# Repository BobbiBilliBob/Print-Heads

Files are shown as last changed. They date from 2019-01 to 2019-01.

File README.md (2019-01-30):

# Print-Heads

## PH_4010
It's a print head for 4010 fans. 

## PH_4010_BLTouch
It's a print head for 4010 fans. This version provides possibility to install BLTouch.
We install this version on printers that we produce by default.

## PH_Sunon35x5_original
It's a print head for Sunon35x5 mm fans. 

## PH_Sunon35x7
It's a print head for Sunon35x5 mm fans. 

# License
Z Bolt printer is released under the [GNU General Public License v3.0.](https://opensource.org/licenses/GPL-3.0)

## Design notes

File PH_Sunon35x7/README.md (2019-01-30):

# Print-Head

Version of print head for the Sunon 35x7mm fans.
This folder contains only those parts that differ from the version for the fans Sunon 35x5mm.
So please find other parts in folder PH_Sunon35x5_Original.

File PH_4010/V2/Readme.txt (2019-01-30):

-Подкорректированы некоторые размеры
-Добавлена полка для вентилятора радиатора
-Добавлена верхняя заглушка вентилятора радиатора
-Крепление E3dv6 оптимизировано под вентилятор 4010 (спасибо @AleksRei)

Винты крепления вентилятора радиатора - М3х16 потай.

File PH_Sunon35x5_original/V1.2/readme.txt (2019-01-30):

разнес пошире "дюзы" обдува детали, чтобы не плавились нагревательным "кубиком". Остальные детали не изменились.

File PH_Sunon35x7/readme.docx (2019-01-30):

Остальные печатные детали такие же, как в версии PH_Sunon35x5_ORIGINAL

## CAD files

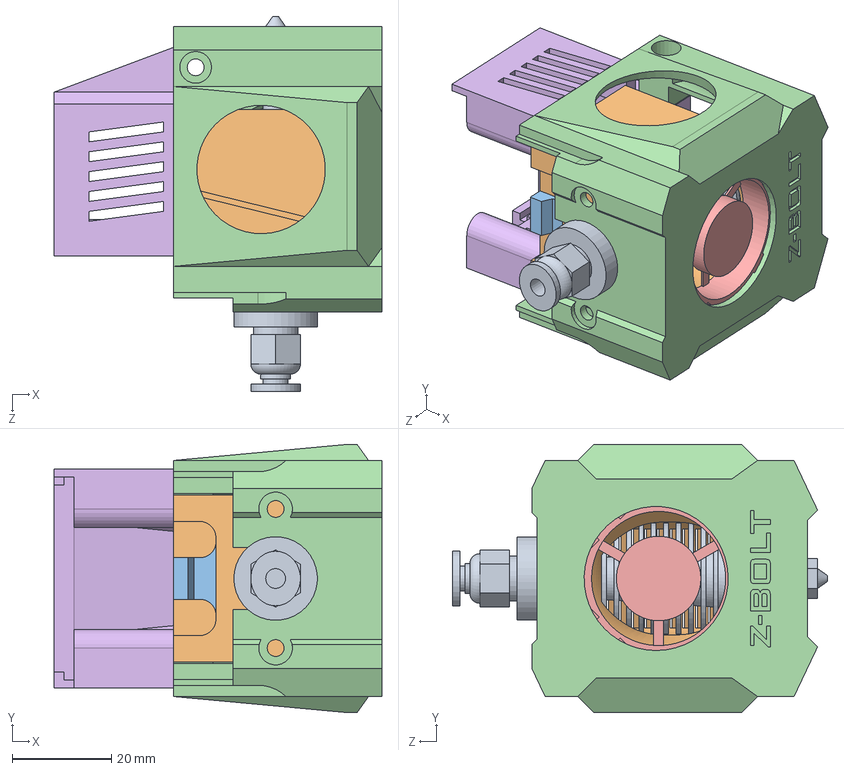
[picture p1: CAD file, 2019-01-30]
PH_Sunon35x5_original/AS_PH_35x5.SLDASM
66.0 x 54.0 x 75.5 mm
e3dv6
e3dv6Mount
fix
PHFront
cooler30-7
PHback

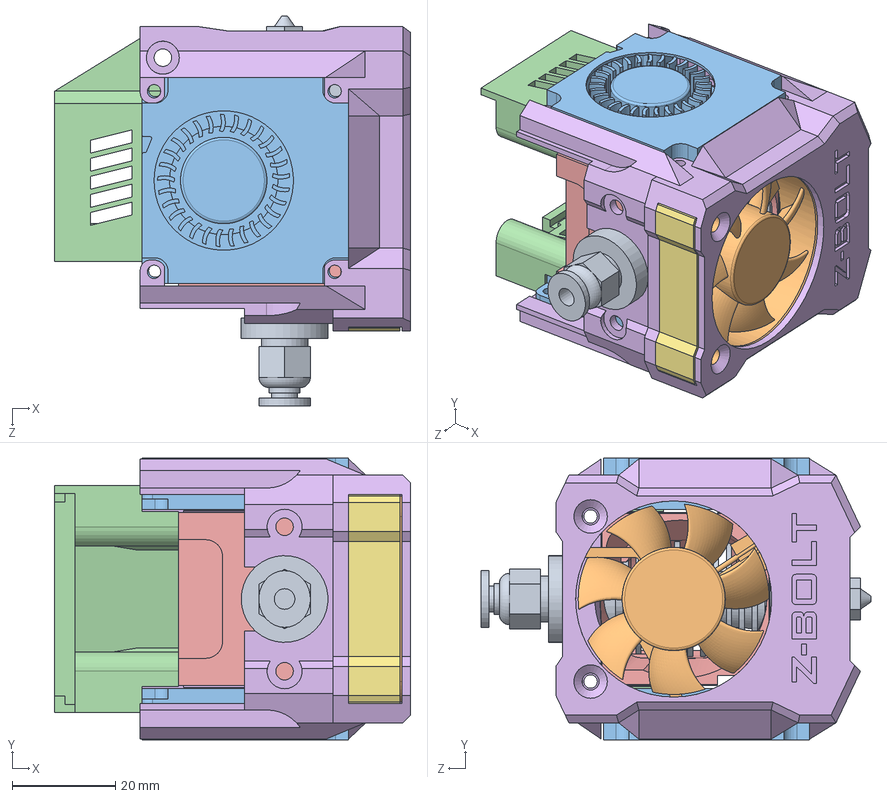
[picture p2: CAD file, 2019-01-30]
PH_4010/V2/src/AS_PH4010_V2.SLDASM
69.0 x 54.6 x 75.5 mm
e3dv6
40x40x10 DC Fan
4010turbo x 2
PHback4010
e3dv6Mount4010
PHFront_4010_V2
VentCover

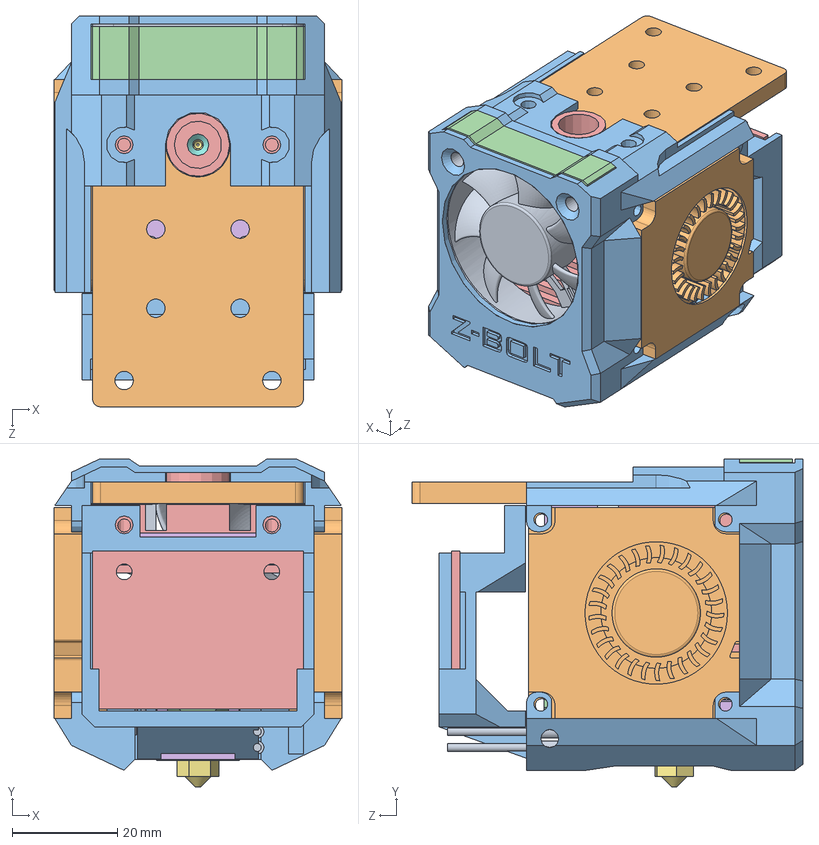
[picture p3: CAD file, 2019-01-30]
PH_4010_custom_radiator/AS_PH4010_V4.SLDASM
54.6 x 62.2 x 74.1 mm
40x40x10 DC Fan
4010turbo x 2
PHFront_4010_V4
VentCover
CustomRadiatorV4
Heatblock
nuzzle
Heatbr
heater
HotEndPlate
PHback4010V4_2
Деталь2
pcb
Костыль А

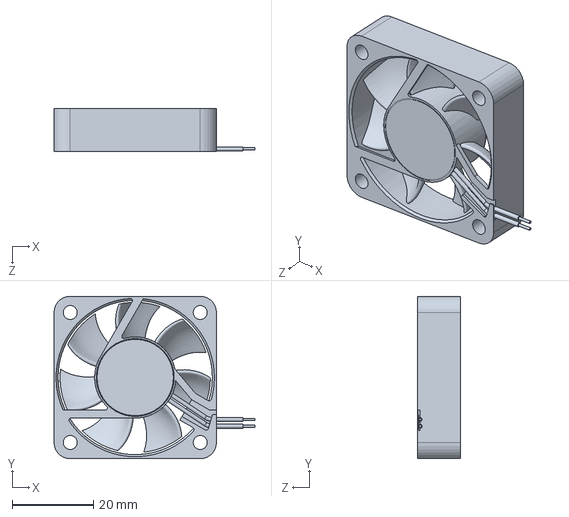
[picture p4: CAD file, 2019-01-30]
PH_4010/V2/src/40x40x10 DC Fan.SLDPRT
49.5 x 40.0 x 10.5 mm

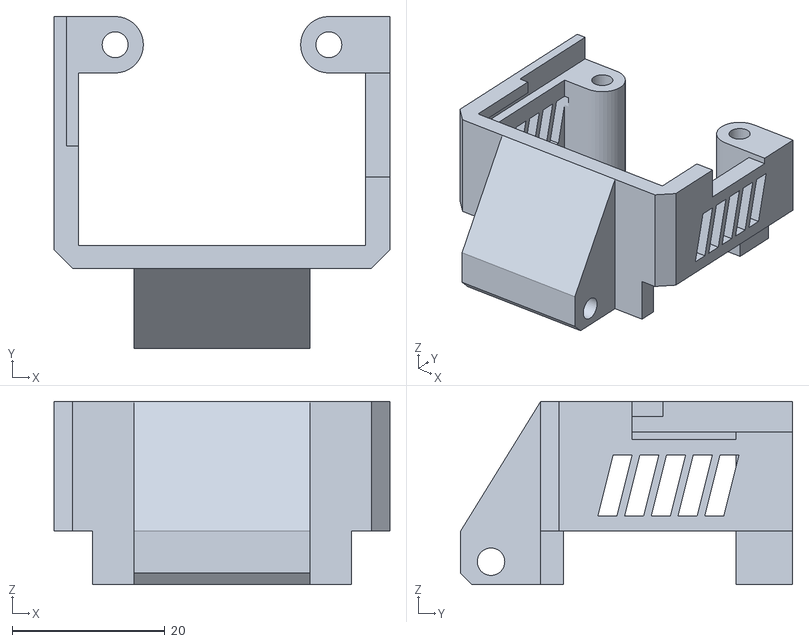
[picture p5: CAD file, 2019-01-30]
PH_4010/V2/STL/PHback4010.STL
44.0 x 43.5 x 24.0

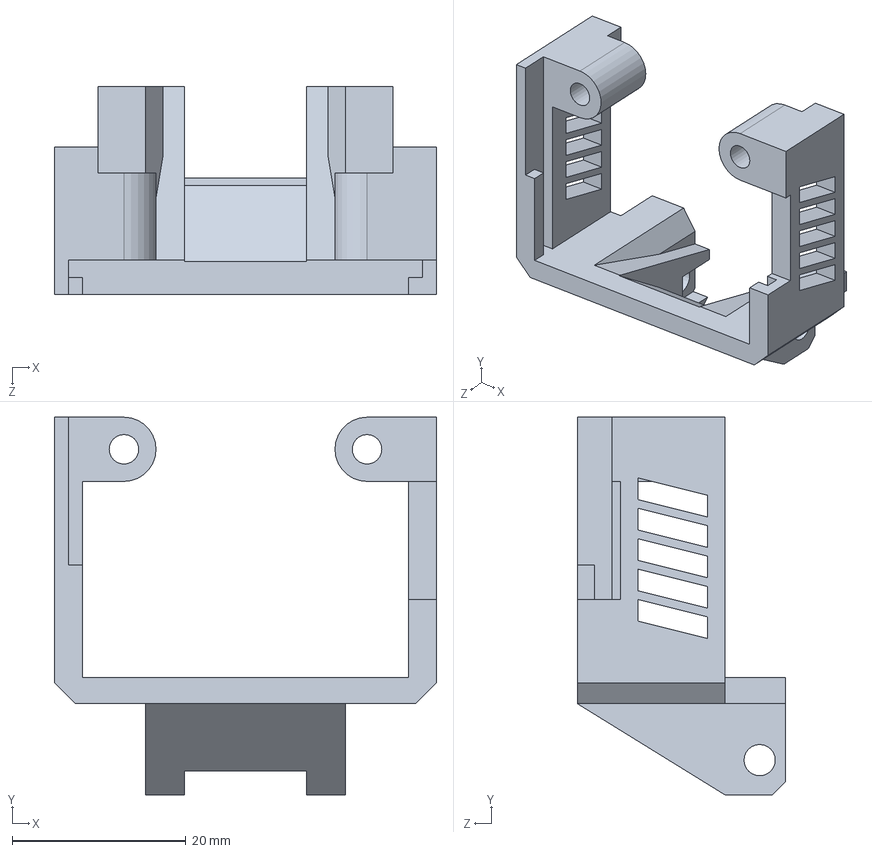
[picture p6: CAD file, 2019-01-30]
PH_4010_BLTouch (from @mivtahim )/src/PHback4010.SLDPRT
44.0 x 43.5 x 24.0 mm

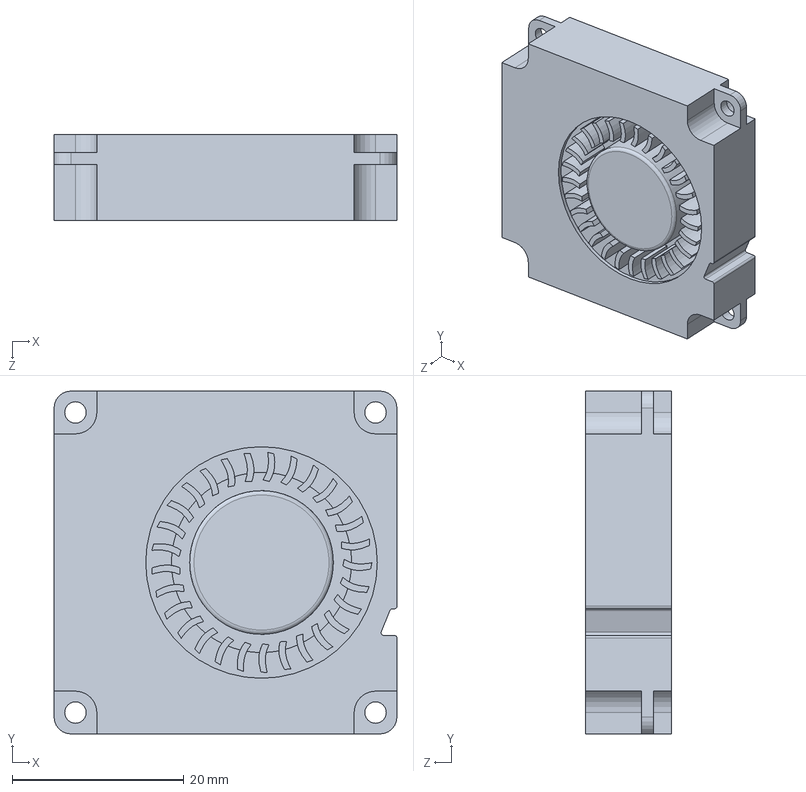
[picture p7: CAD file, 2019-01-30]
PH_4010_custom_radiator/4010turbo.SLDPRT
40.0 x 40.0 x 10.0 mm

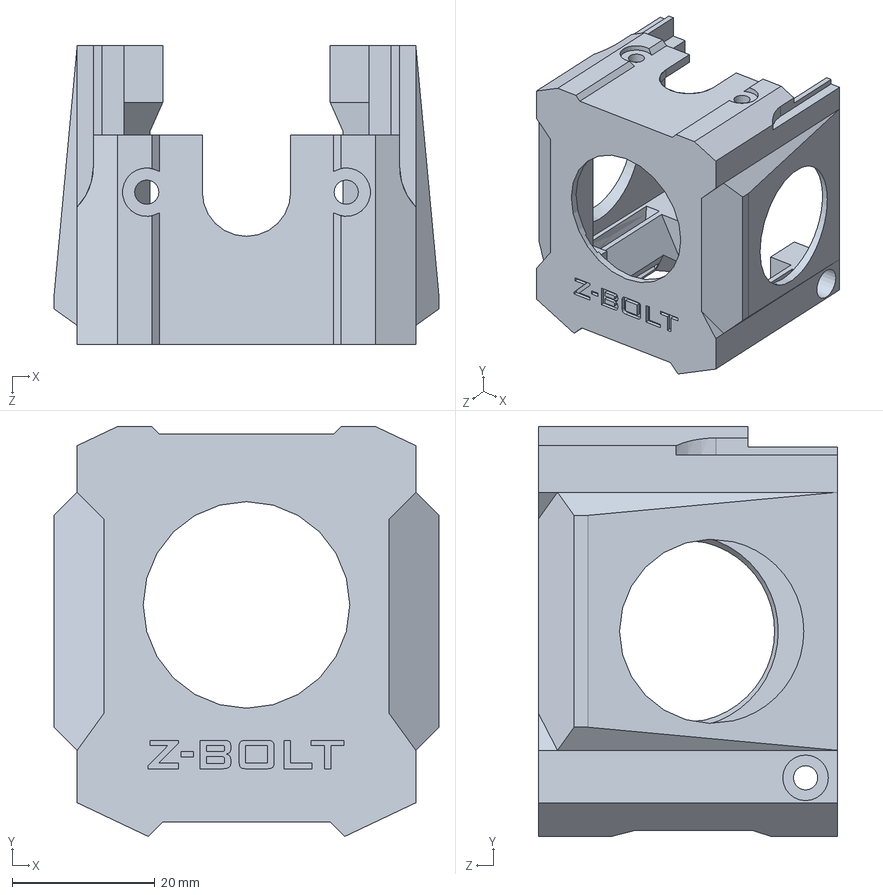
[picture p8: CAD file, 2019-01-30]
PH_Sunon35x5_original/V1.2/PHFront_V1.2.SLDPRT
54.0 x 57.5 x 42.0 mm

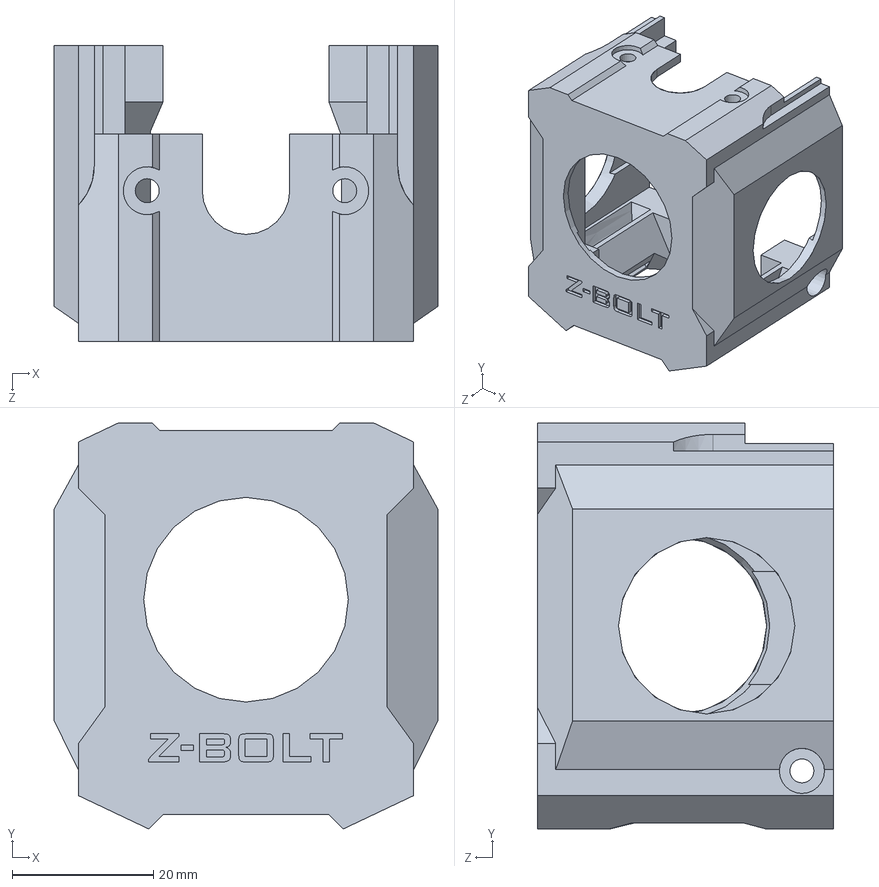
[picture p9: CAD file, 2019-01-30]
PH_Sunon35x7/PHFront_Sunon7mm.SLDPRT
54.4 x 57.5 x 42.0 mm

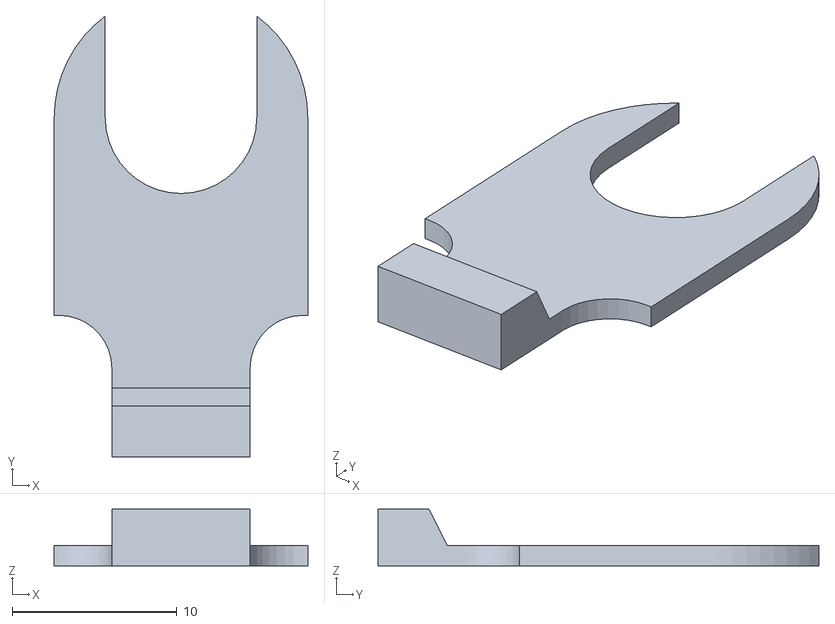
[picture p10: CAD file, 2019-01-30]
PH_4010/V2/STL/fix.STL
15.4 x 26.8 x 3.44

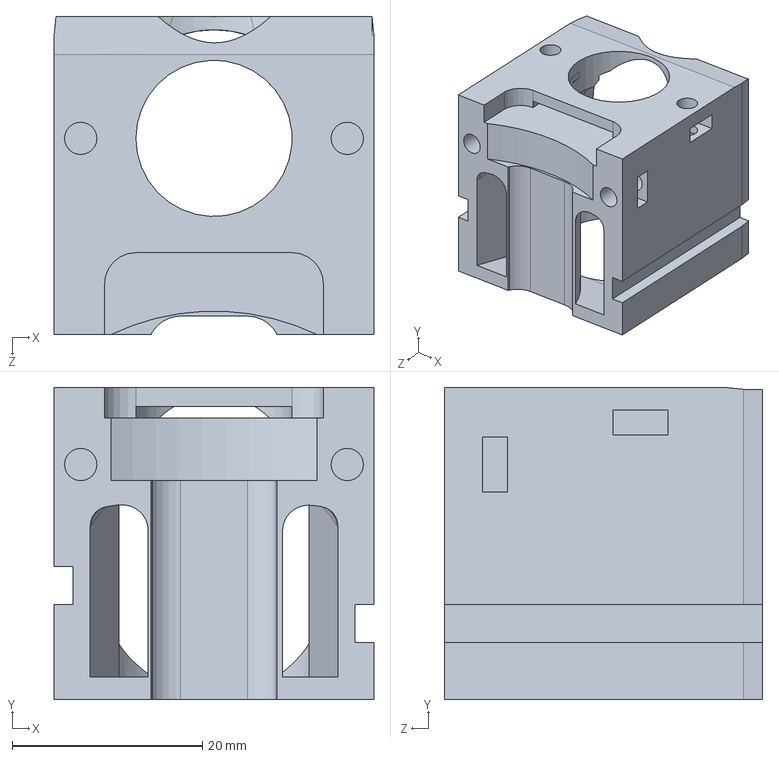
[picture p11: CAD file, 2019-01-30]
PH_4010_BLTouch (from @mivtahim )/src/e3dv6Mount4010.SLDPRT
33.6 x 32.8 x 33.4 mm

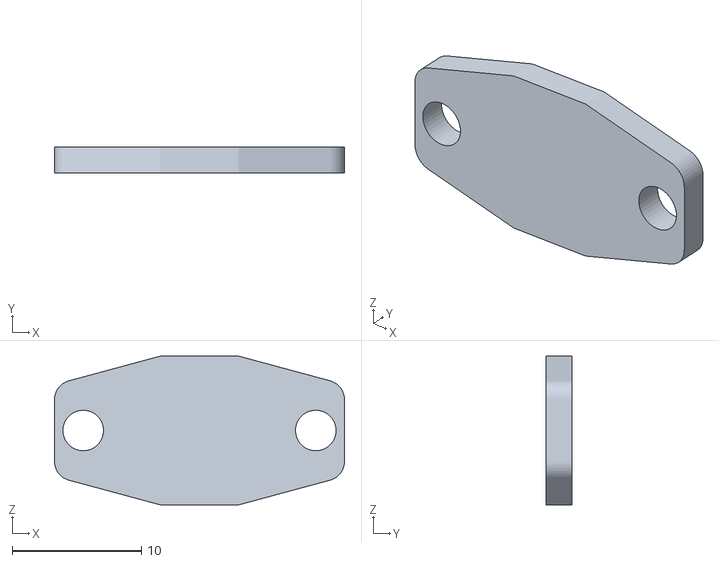
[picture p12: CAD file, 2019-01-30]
PH_4010_BLTouch (from @mivtahim )/STL/opravka_A_v2.STL
22.4 x 2.00 x 11.5

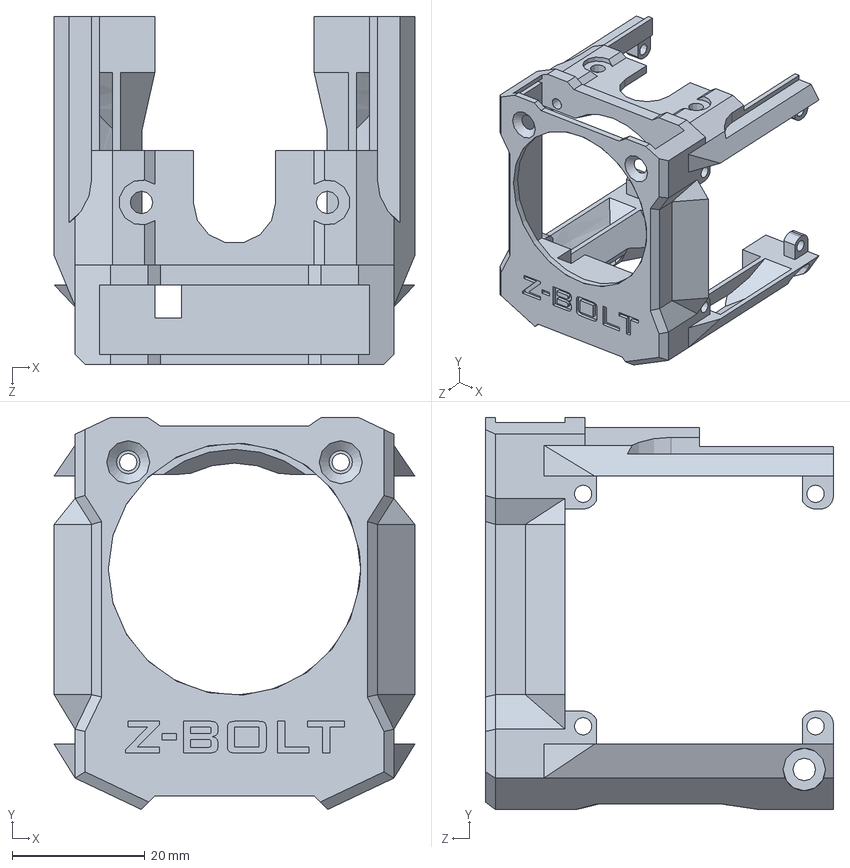
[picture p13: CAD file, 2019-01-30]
PH_4010_custom_radiator/PHFront_4010_V4.SLDPRT
54.3 x 59.0 x 52.4 mm

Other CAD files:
PH_4010_BLTouch (from @mivtahim )/STL/BLTPH_PHback4010.STL
PH_4010/V2/src/PHback4010.SLDPRT
PH_Sunon35x5_original/PHFront.SLDPRT
PH_4010/V2/STL/PHFront_4010_V2.STL
Old Versions/PH_Sunon35x7 v0.1/PHback.STL
Old Versions/PH_Sunon35x7 v0.1/fix.STL
PH_4010/V1/STL/PHFront_4010.STL
PH_4010/V1/STL/e3dv6Mount4010.STL
PH_4010/V1/src/AS_PH4010.SLDASM
PH_4010/V1/src/PHFront_4010.SLDPRT
PH_4010/V1/src/PHback4010.SLDPRT
PH_4010/V1/src/e3dv6.SLDPRT
PH_4010/V1/src/e3dv6Mount4010.SLDPRT
PH_4010/V1/src/fix.SLDPRT
PH_4010/V2/STL/VentCover.STL
PH_4010/V2/STL/e3dv6Mount4010.STL
PH_4010/V2/src/PHFront_4010_V2.SLDPRT
PH_4010/V2/src/VentCover.SLDPRT
PH_4010/V2/src/e3dv6.SLDPRT
PH_4010/V2/src/e3dv6Mount4010.SLDPRT
PH_4010/V2/src/fix.SLDPRT
PH_4010_BLTouch (from @mivtahim )/STL/BLTPH_Holder.STL
PH_4010_BLTouch (from @mivtahim )/STL/BLTPH_PHFront_4010_V2.STL
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

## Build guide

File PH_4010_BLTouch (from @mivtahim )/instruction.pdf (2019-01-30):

1. СБОРКА

Модель "opravka_A_v2" (на скрине не конкретно она, но принцип сохраняется) необходима для срезания ушей с корпуса сенсора:

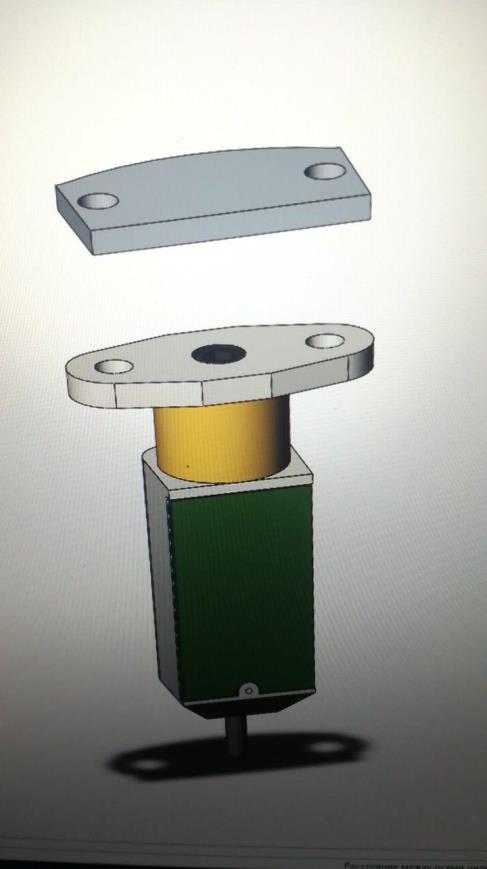
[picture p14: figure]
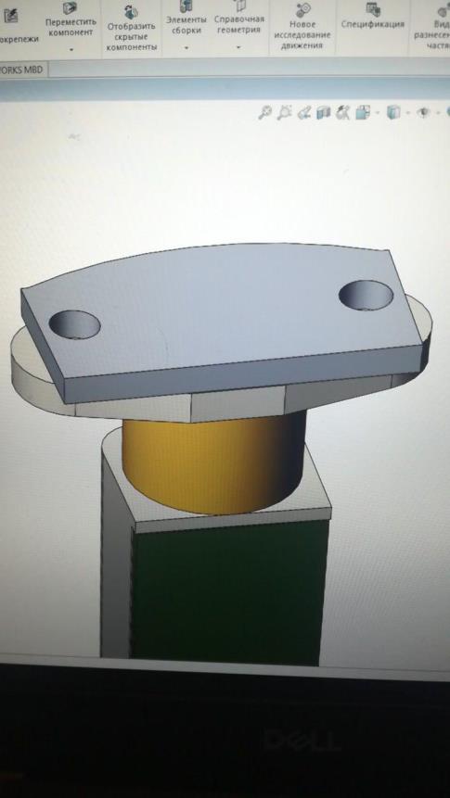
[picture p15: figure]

Центруем и как следует затягиваем, не до скрипа, конечно. Но чтоб не сместилась:

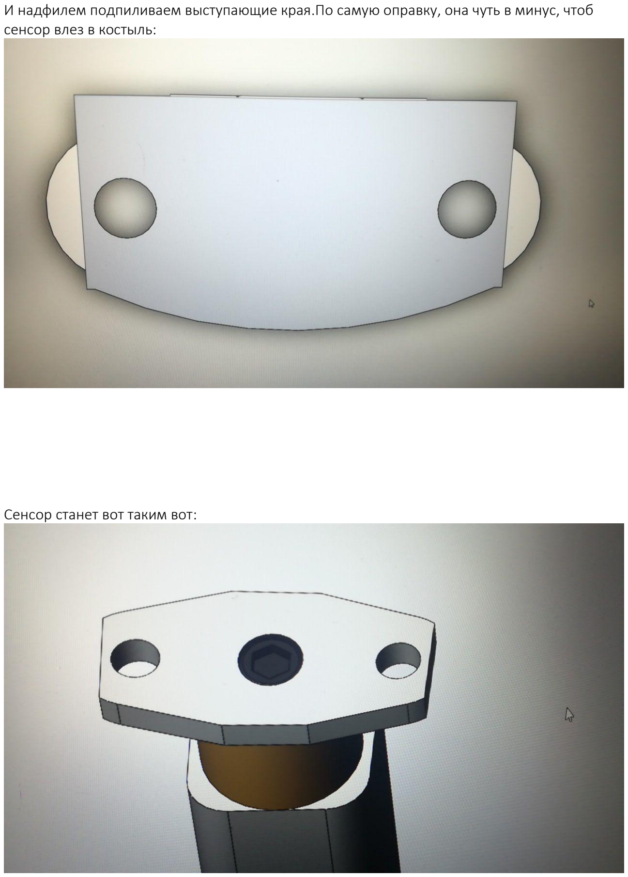
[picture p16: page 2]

И надфилем подпиливаем выступающие края.По самую оправку, она чуть в минус, чтоб сенсор влез в костыль:

Сенсор станет вот таким вот:

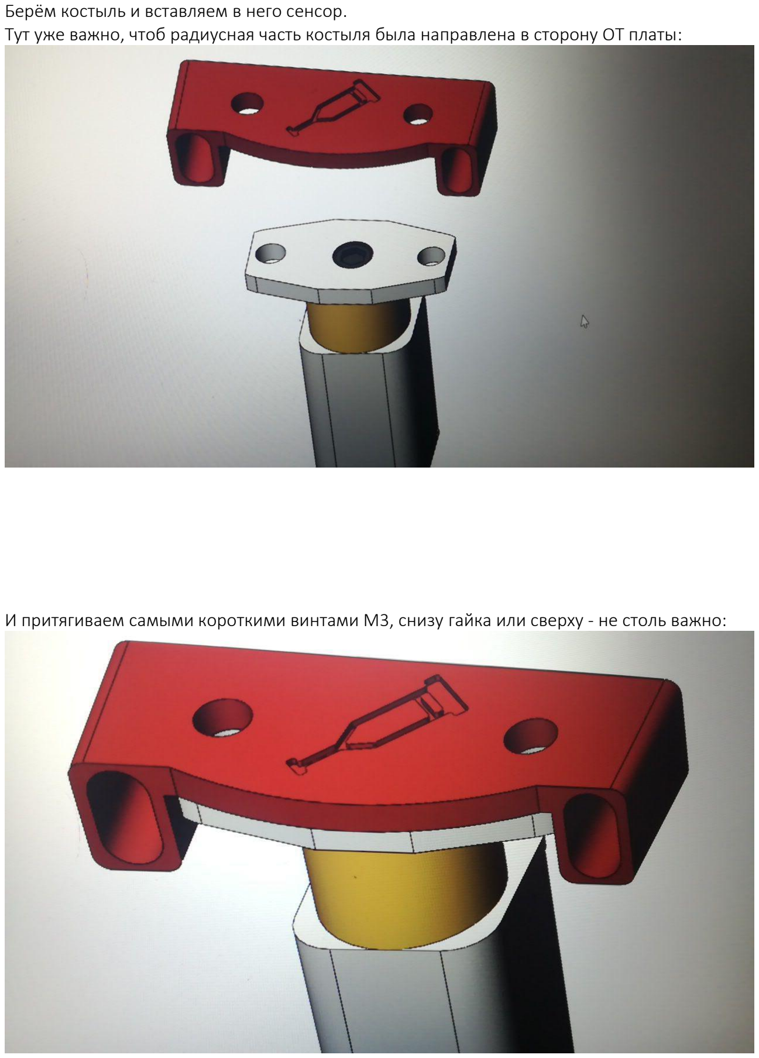
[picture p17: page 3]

Берём костыль и вставляем в него сенсор.
Тут уже важно, чтоб радиусная часть костыля была направлена в сторону ОТ платы:

И притягиваем самыми короткими винтами М3, снизу гайка или сверху - не столь важно:

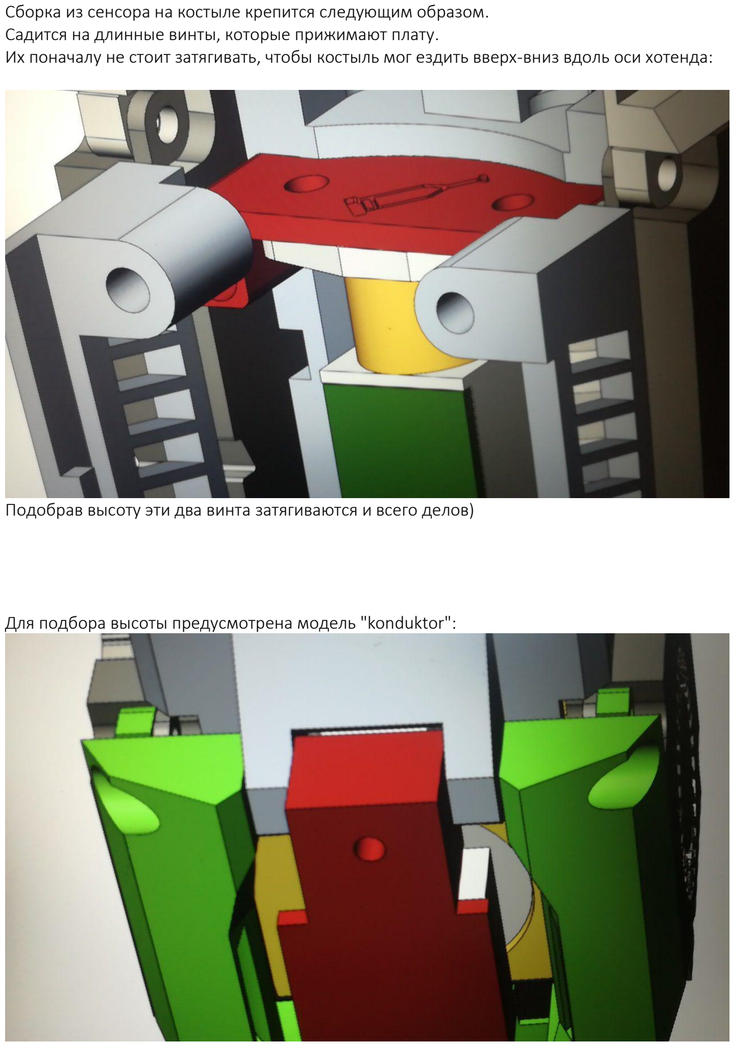
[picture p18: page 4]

Сборка из сенсора на костыле крепится следующим образом.
Садится на длинные винты, которые прижимают плату.
Их поначалу не стоит затягивать, чтобы костыль мог ездить вверх-вниз вдоль оси хотенда:

Подобрав высоту эти два винта затягиваются и всего делов)

Для подбора высоты предусмотрена модель "konduktor":

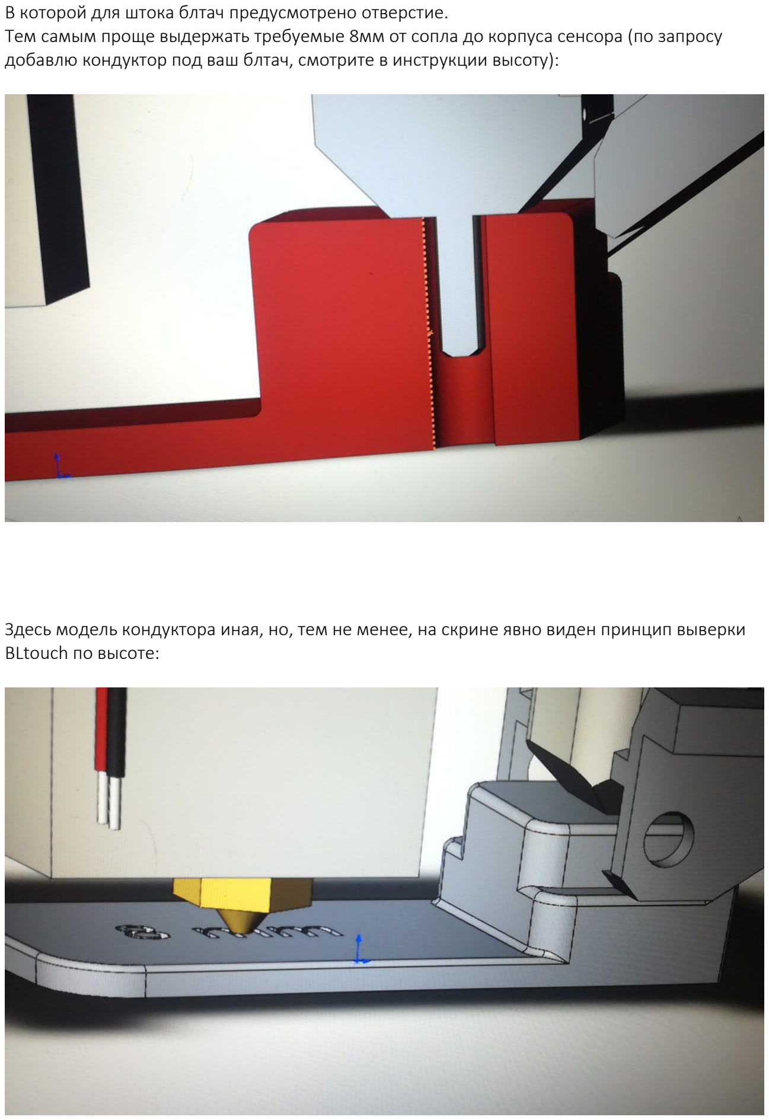
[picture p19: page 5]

В которой для штока блтач предусмотрено отверстие.
Тем самым проще выдержать требуемые 8мм от сопла до корпуса сенсора (по запросу добавлю кондуктор под ваш блтач, смотрите в инструкции высоту):

Здесь модель кондуктора иная, но, тем не менее, на скрине явно виден принцип выверки BLtouch по высоте:

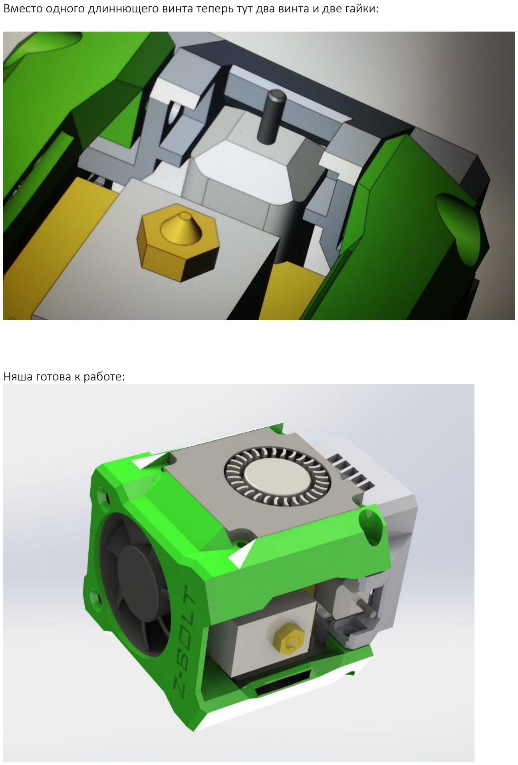
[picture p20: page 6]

Вместо одного длиннющего винта теперь тут два винта и две гайки:

Няша готова к работе:

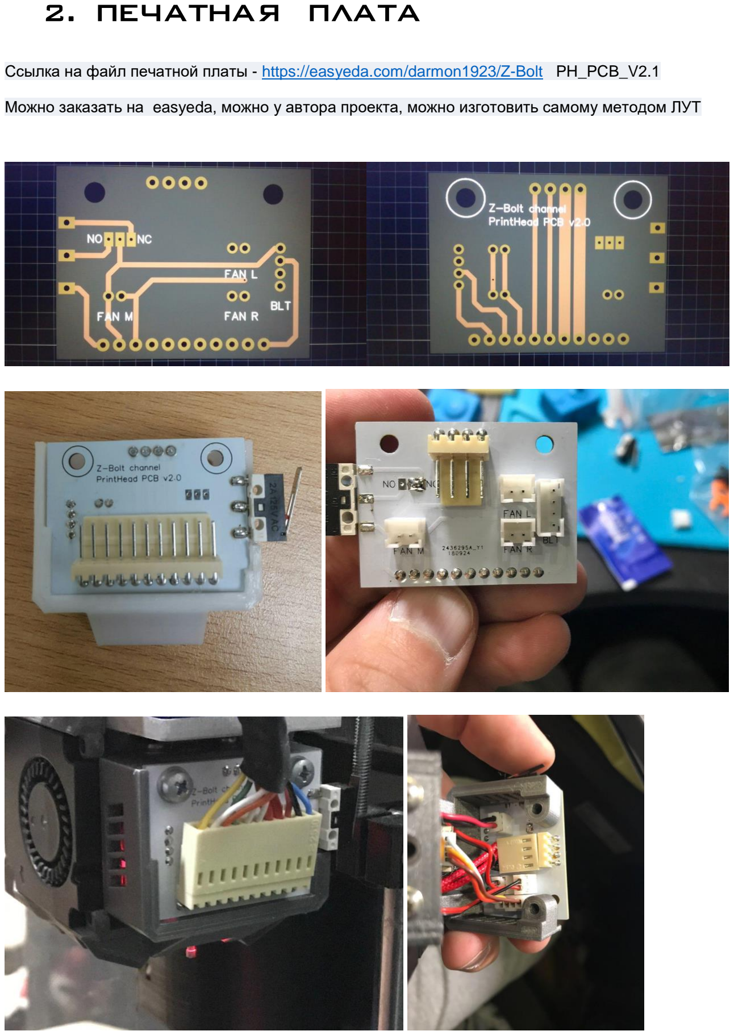
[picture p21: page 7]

2. Печатная плата

Ссылка на файл печатной платы - https://easyeda.com/darmon1923/Z-Bolt PH_PCB_V2.1

Можно заказать на easyeda, можно у автора проекта, можно изготовить самому методом ЛУТ

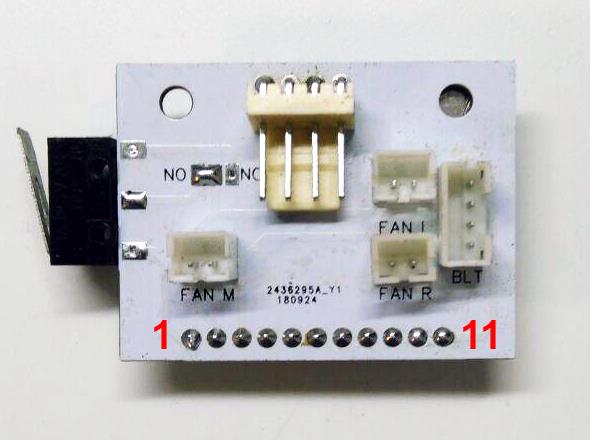
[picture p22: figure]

1 – Сигнал концевика X.
2 – 0В.
3 - +12/24В (в зависимости от выбора блока питания и вентиляторов) 4 – Нагреватель хотэнда 1 (полярность не имеет значения)
5 – Нагреватель хотэнда 2 (полярность не имеет значения)
6 – Термистор хотэнда 1 (полярность не имеет значения)
7 – Термистор хотэнда 2 (полярность не имеет значения) 8 - FAN- (ШИМ для вентиляторов обдува модели)
9 – Сигнал концевика Zmin (bltouch)
10 – Cигнал автоуровня (bltouch)
11 - +5В (bltouch)

3. настройка

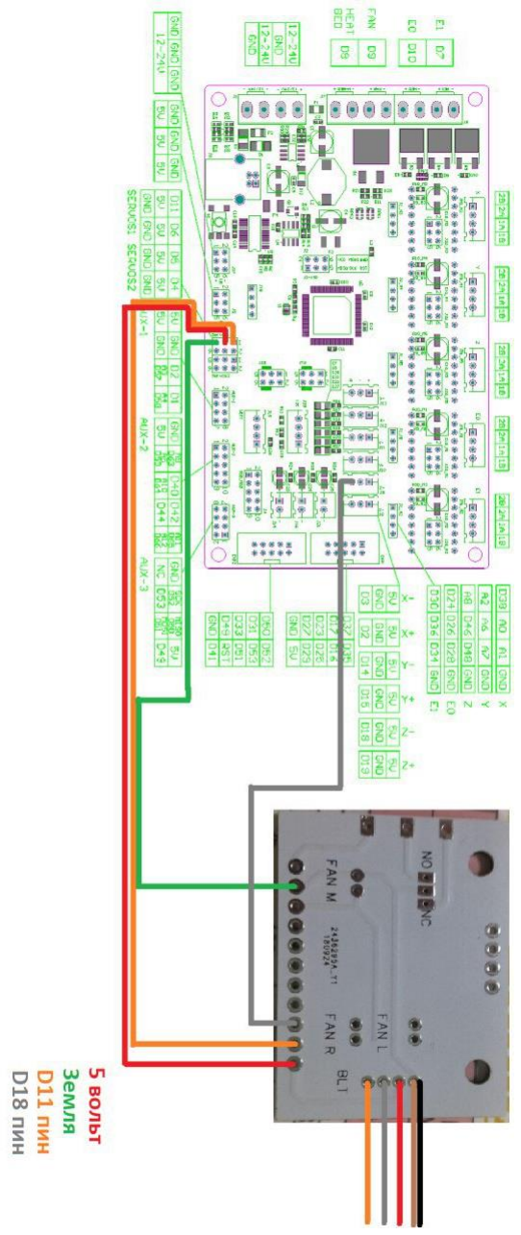
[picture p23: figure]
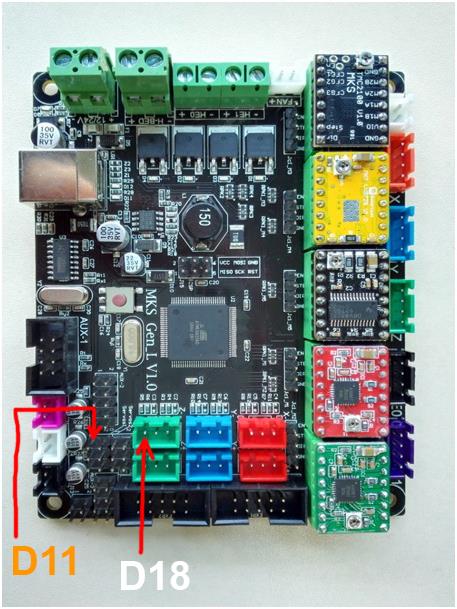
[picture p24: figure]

MKS Gen 1.4 | MKS Gen L

справа от платы выходят из 4х контактов 5 проводов - это к блтач подписаные цвета - то что в косе идет от мкс к платке ПГ
Серый провод прошу считать белым
то что на схеме - ориентир и не более того)

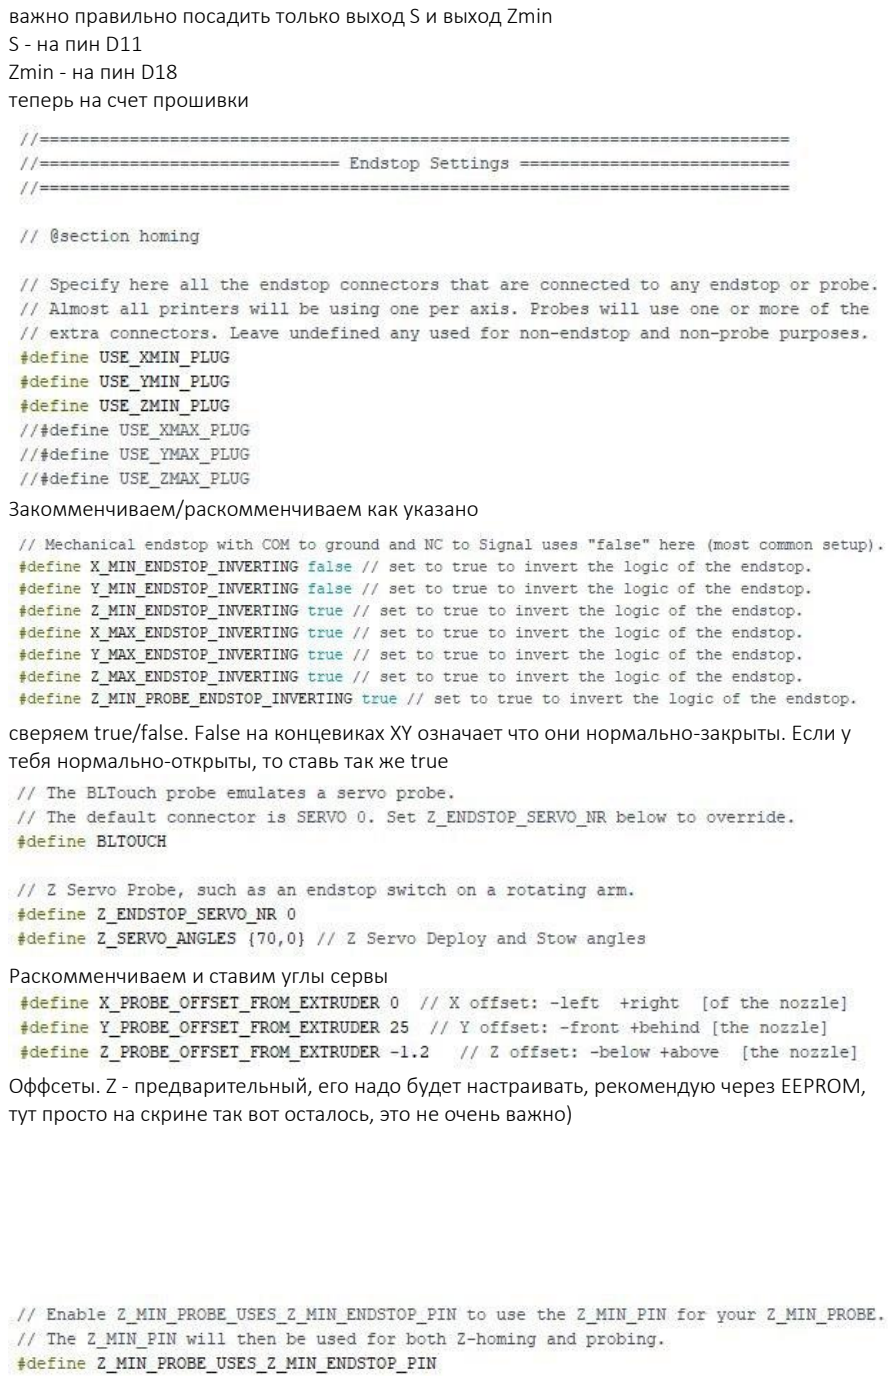
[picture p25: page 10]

важно правильно посадить только выход S и выход Zmin S - на пин D11
Zmin - на пин D18
теперь на счет прошивки

Закомменчиваем/раскомменчиваем как указано

сверяем true/false. False на концевиках XY означает что они нормально-закрыты. Если у тебя нормально-открыты, то ставь так же true

Раскомменчиваем и ставим углы сервы

Оффсеты. Z - предварительный, его надо будет настраивать, рекомендую через EEPROM, тут просто на скрине так вот осталось, это не очень важно)

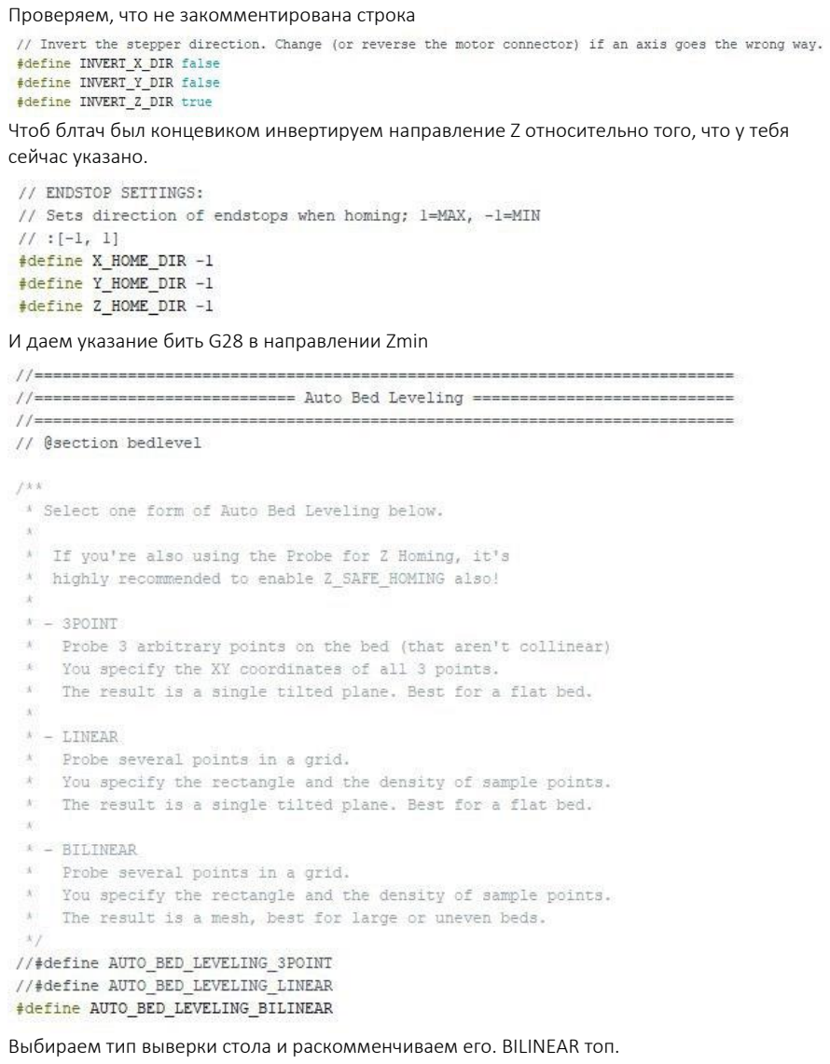
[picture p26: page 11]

Проверяем, что не закомментирована строка

Чтоб блтач был концевиком инвертируем направление Z относительно того, что у тебя сейчас указано.

И даем указание бить G28 в направлении Zmin

Выбираем тип выверки стола и раскомменчиваем его. BILINEAR топ.

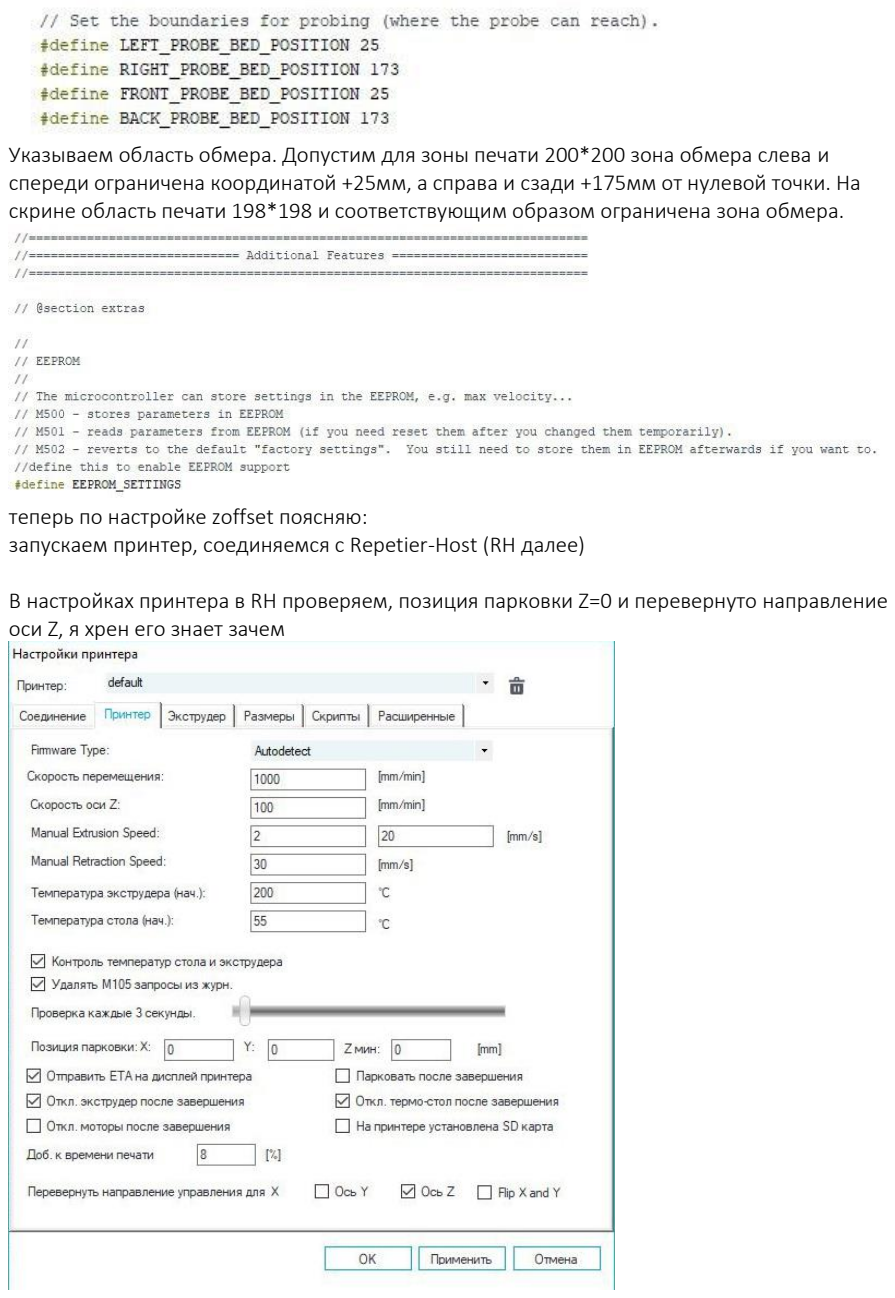
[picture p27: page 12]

Указываем область обмера. Допустим для зоны печати 200*200 зона обмера слева и спереди ограничена координатой +25мм, а справа и сзади +175мм от нулевой точки. На скрине область печати 198*198 и соответствующим образом ограничена зона обмера.

теперь по настройке zoffset поясняю:
запускаем принтер, соединяемся с Repetier-Host (RH далее)

В настройках принтера в RH проверяем, позиция парковки Z=0 и перевернуто направление оси Z, я хрен его знает зачем

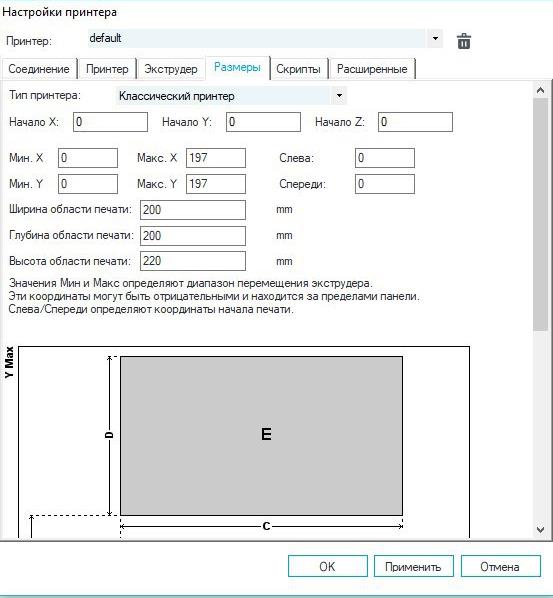
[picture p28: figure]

И что начало Z=0
Соединяемся с принтером, шлем в терминал G28, рука тем временем на выключателе принтера, на всякий случай
Принтер должен отбить концевики XY и, выпустив щуп BLtouch, отбить Zmin
Если получилось - все хорошо, можно расслабиться
Обнуляешь оффсет (M851 Z0 в терминале)
Ставишь каретку в центр стола (G01 X100 Y100 F3000 в терминале для области 200*200) Бьешь Zmin (G28 Z0 в терминале)
Подводишь сопло к столу по миллимеру/десятке кнопками в RH
Смотришь на то, что получается: координата по Z=0 а сопло высоко над столом.
Это отлично и удобно.
Забиваешь в терминал завышенный оффсет по Z. Допустим на глаз сопло в 3мм над столом
- ставишь оффсет 5мм, последовательно вводя в терминал:
M851 Z-5
M500
G28
G01 X100 Y100 F3000

Повторяешь подвод сопла к столу, твоя задача поймать тот момент когда бумажка офисная с небольшим натягом ходила между соплом и столом. Это высота по Z=0.1

Теперь матан: Сопло прижимает бумажку, координата по Z 1.2мм. Просто для примера, само собой.
То есть оффсет корректный 5-1,2+0.1=3,9мм

В терминал последовательно:
M851 Z-3.9
M500
G28
G01 X100 Y100 F3000

Проверяешь, снова подведя сопло к столу. Должно все стать четко.

Чтоб порадовать себя запускаешь калибровку стола (G29 в терминале) и смотришь, как принтер за тебя настраивает уровень стола)
Теперь в старт-код слайсера добавляешь перед печатью но после G28 и нагревов волшебную команду G29
И все, собственно говоря, стол больше настраивать не нужно.
